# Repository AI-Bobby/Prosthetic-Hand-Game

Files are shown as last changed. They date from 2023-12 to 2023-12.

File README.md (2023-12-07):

# Prosthetic-Hand-Game

This project consists of the mechanical design, electrical design, software design, and using the system of an articulating hand that plays Rock-Paper-Scissors with the user. The hand also has the built-in functionality to control the fingers individually (the ring and pinky finger move together). This was designed around an interest in robotic prosthetics and exoskeletons. 

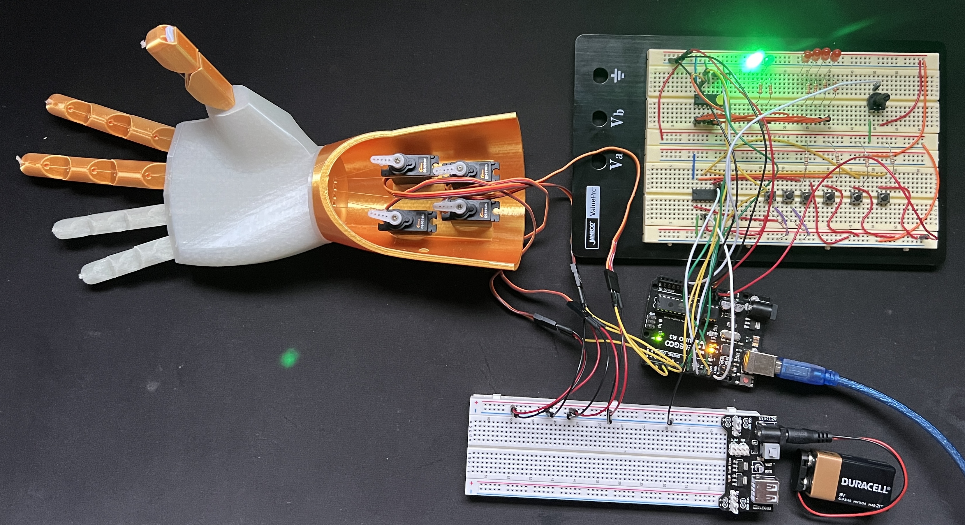
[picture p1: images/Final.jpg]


## 1. Mechanical Design

The mechanical design was based on a normal human hand. The file was modified from an existing design by grossrc on Thingiverse (https://www.thingiverse.com/thing:1691704). Modifications were done by removing the supports that were originally in the design for the circuits. This allows for the arm portion which holds the 4 servo motors used in this design to have free movement when actuating. The .stl files can be seen in the design folder. The 3D printed hands can be seen below:

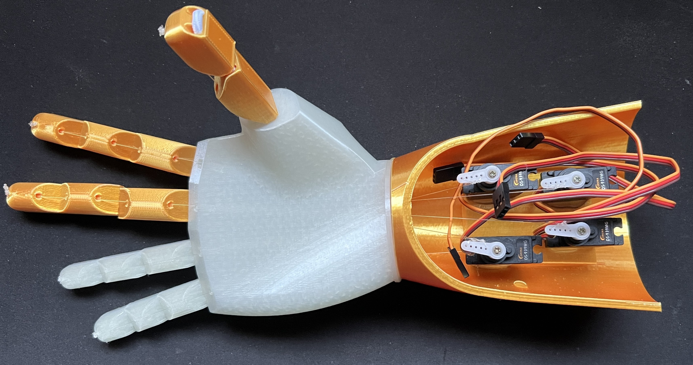
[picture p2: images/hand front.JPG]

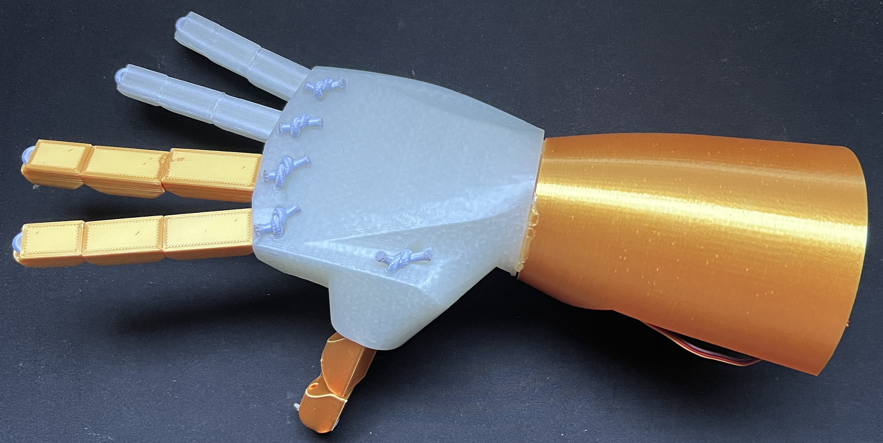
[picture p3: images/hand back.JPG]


The fingers are articulated by 2 things, the fishing line attached to the servo motors, and the nylon string running through the fingers and attached to the hand. The nylon string acts like a tendon that holds the finger in place when not in use. The fishing line is pulled by the servo-motors when they rotate to cause a "muscle" contraction causing the finger(s) to close. The servo motors were positioned to ensure that there would be no collision when the fingers are actuating. The position and the connections of the servo motors can be seen in the image below:

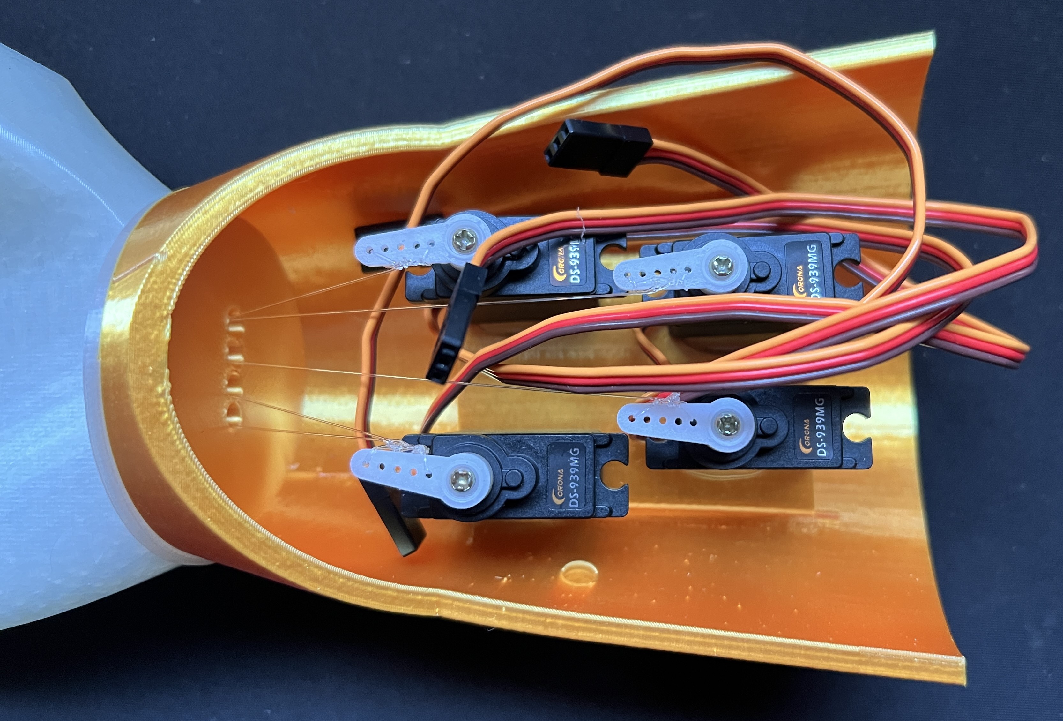
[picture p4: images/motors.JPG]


### BOM

|Part|Description|Qty.|
|:---:|:---|:---:|
|Arduino Uno|Main computational system being used.|1|
|3D Printed Hand|Hand that was 3D printed.|1|
|Nylon String|Nylon string used as tendons in the hand.|5|
|10lb. Test Fishing Line|Fishing line used to act like muscles in the hand.|5|
|DS939MG Digital Servo|Servo motors controlling the fingers.|4|
|CD74HC4051E|8 to 1 Multiplexer reading the control buttons.|1|
|SN74AHC595|8-bit Shift Register controlling the LEDs.|1|
|LED|LEDs giving feedback to the user.|6|
|Button|Buttons used to change output seen by the user.|6|
|220Ω Resistor|Resistors used to limit current to LEDs.|6|
|10kΩ Resistor|Pull-down resistors used with the buttons.|6|
|10kΩ Potentiometer|Potentiometer used to control the position of the servos.|1|
|9V Battery|Battery to supply power to the servo motors.|1|
|Wires|Used to connect components.|58|
|Breadboard|Breadboards used for connecting components together.|3|
|MB102 Power Module|Power Supply Module to supply power to the servos from the 9V battery.|1|
|USB Power Cable|Cable to provide power to the Arduino.|1|

## 2. Electrical Design

For the electrical design an Arduino Uno was used as the microcontroller to run the processes for controlling the hand. The Arduino Uno only has 13 I/O digital pins and 6 analog pins. Based on the original design there would be a total of 6 buttons, 6 LEDs, 4 servo-motors, a potentiometer. Based on these components 16 digital pins would have been needed so the multiplexer and the shift register were added which reduces the number of pins needed. Now the number of digital pins is reduced to 12 digital pins with the shift-register being used for the LEDs and the multiplexer being used for the buttons. The system's wiring diagram can be seen below:

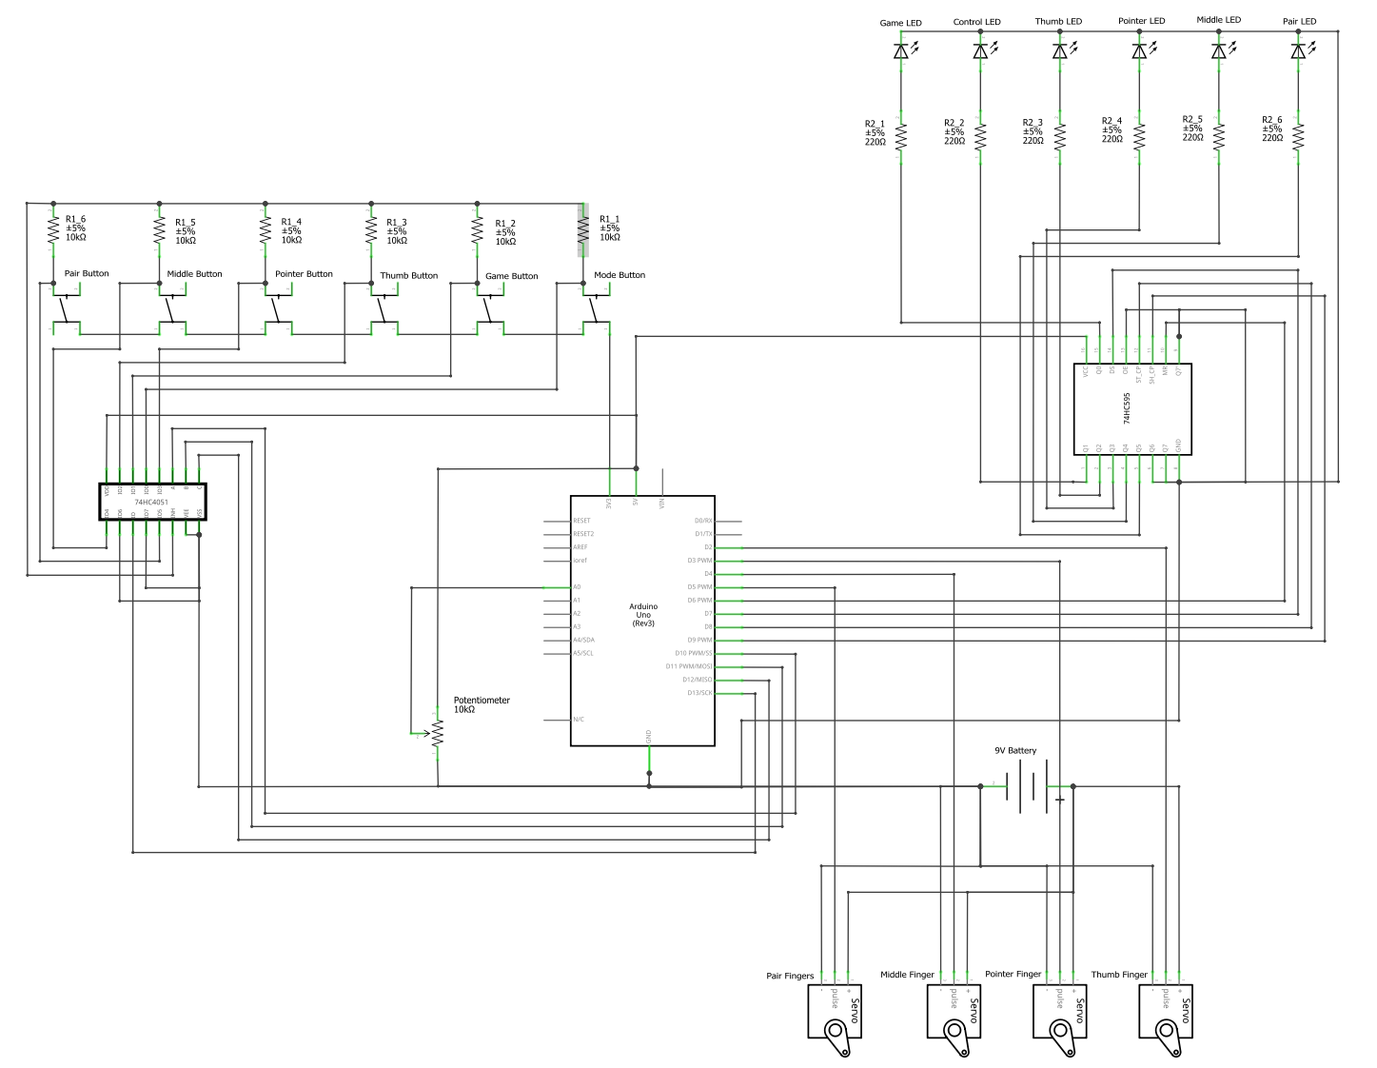
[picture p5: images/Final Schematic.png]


The servo motors are connected to their own separate 9V battery to allow for there to be no current drop if all four of the servo motors are active at the same time. This schematic also shows how the multiplexer and the shift-register are wired to help reduce the number of input wires to the Arduino Uno. The multiplexer has 6 buttons each with their own respective function attached that reads LOW. The buttons have 10kΩ pull-down resistors attached to limit current going into the Arduino and when the button is pressed the Arduino will read HIGH. 

## 3. Software Design

The software design for this system is a simplistic streamlined process to allow for reduced memory usage and ease of use. The file main.cpp in the src folder contains the defined functions of the software running on the Arduino. The code uses enumeration to select the specific case for the multiple switch cases determined by the buttons. Within the code the shift register is used to shift binary strings representing the locations of each of the LEDs to light up based on the specific function being performed. The multiplexer is referenced each loop of the Arduino code and checks each LED to see if a button has been pressed. The pressing of a button influences the specific binary string that is then sent to the shift register to change the LEDs that are lit. The button also determines the mode the system is in as well as the specific finger being controlled.

The code consists of 2 modes and 5 functions: Game, Control, setup, loop, gameMove, updateSystem, and shifter. Each function has its respective repetitive functionality. The mode Game allows for the mode button and the random selection of the hand shape button to be pressed. The game button when pressed uses the microcontroller's clock to get a random seed on each loop so that the selection of the hand shape is completely random. In the Control mode the individual fingers are controlled based on a mapping of the potentiometers analog input and the angles of each servo-motor respectively.  Setup sets the needed pins to their respective I/O setting. Loop checks the button to see if one has been pressed as well as when in the control mode allows for the movement of the fingers based on the reading from the potentiometer mapped to the angles of the servo-motors. The gameMove function randomly chooses the shape for the hand to be performed by the hand and also reset the hand if changed from the control mode to the game mode. The updateSystem function handles the different functionalities based on the button that was pressed. Shifter is a function that sends the binary string to the shift register to change the LED output. 

## 4. Using System

Once the system is wired and powered the system will be in the initial state of Game mode. There are two buttons that have functionality while in Game mode, the game button and the mode button. The game button will cause the hand to give a random hand shape from the selection of Rock, Paper, or Scissors. The mode button will switch the mode from Game to Control or Control to Game based on current state. When the mode is changed the LEDs will change color. The green LED represents game mode, the blue LED represents the control mode and the red LEDs represent the finger being controlled. The finger buttons can be pressed while in game mode but will not change the system into a new state unless in the Control mode. When in control mode the finger buttons can be pressed and this will change the finger being used. The potentiometer can then be used to control the position of the servo which controls the fingers position. If the game button is pressed then nothing will happen because the system is in control mode. The buttons and LEDs can be seen labeled in the wiring schematic above and in the system image below:

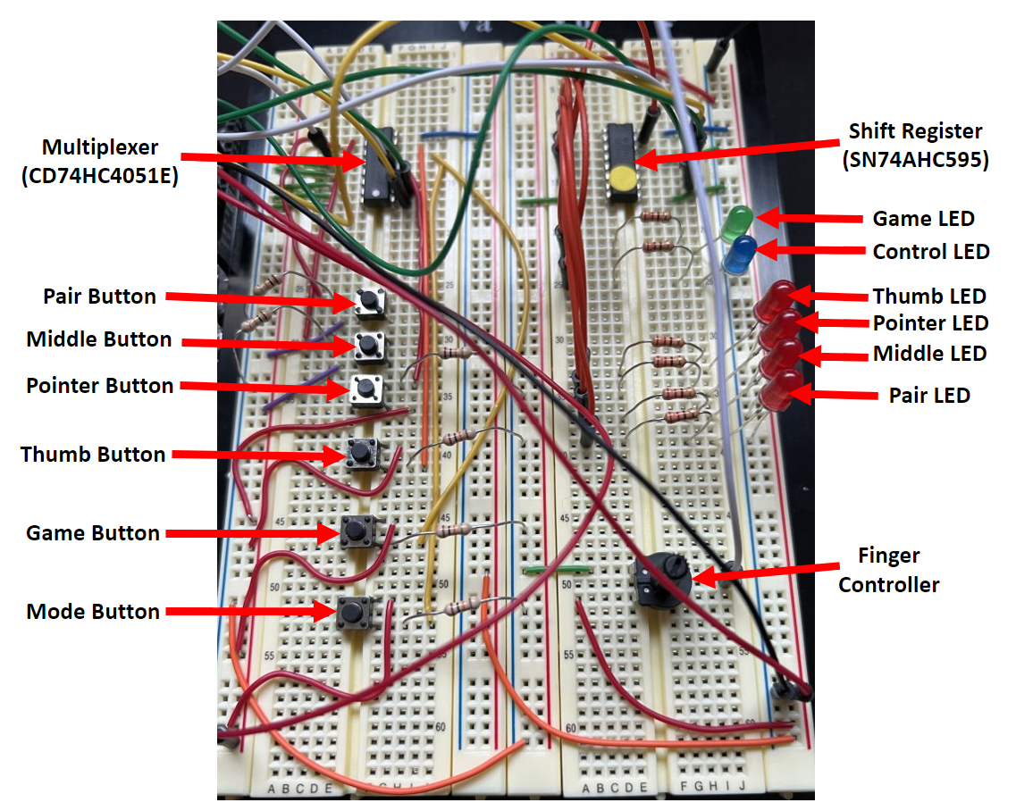
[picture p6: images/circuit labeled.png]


### 4.1 Limitations

The current system has 2 limitations:
1) It was found that the lifespan on a 9V battery is very short because the servo motors when all in use can draw up to ~1A of current which the 9V battery that has 540mAh can not sustain. To circumvent this issue a 5V power supply at 2A was used and allowed for the use of the system without any current drops.
2) During the contraction of the fingers where they should close the fingers do actuate but they do not fully close as a normal hand would. This is caused by the distance of actuation by the motor not being sufficient to fully pull the finger. This can be fixed by either using a longer motor arm horn or using a different actuator. An actuator that could give a larger actuation distance would be a linear actuator where rotation would not have to be considered. The tension that is on the fishing line also plays an effect. Fishing line has an elastic characteristic that needs to be loaded to allow for the actuation of the motor to be seen by the finger. This could be fixed by introducing a string that has much less elasticity.

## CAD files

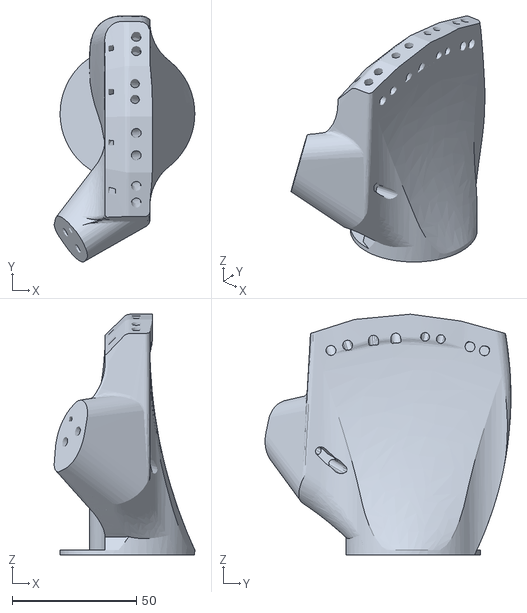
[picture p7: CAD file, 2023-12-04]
design/Hand.stl
56.5 x 98.9 x 96.8

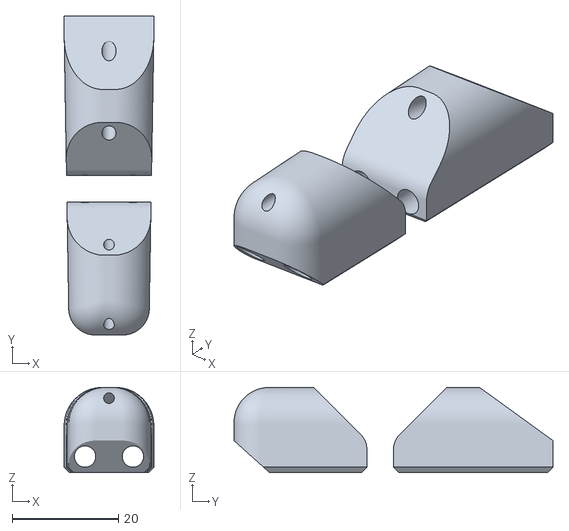
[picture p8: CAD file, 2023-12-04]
design/Thumb.stl
17.0 x 60.0 x 16.0

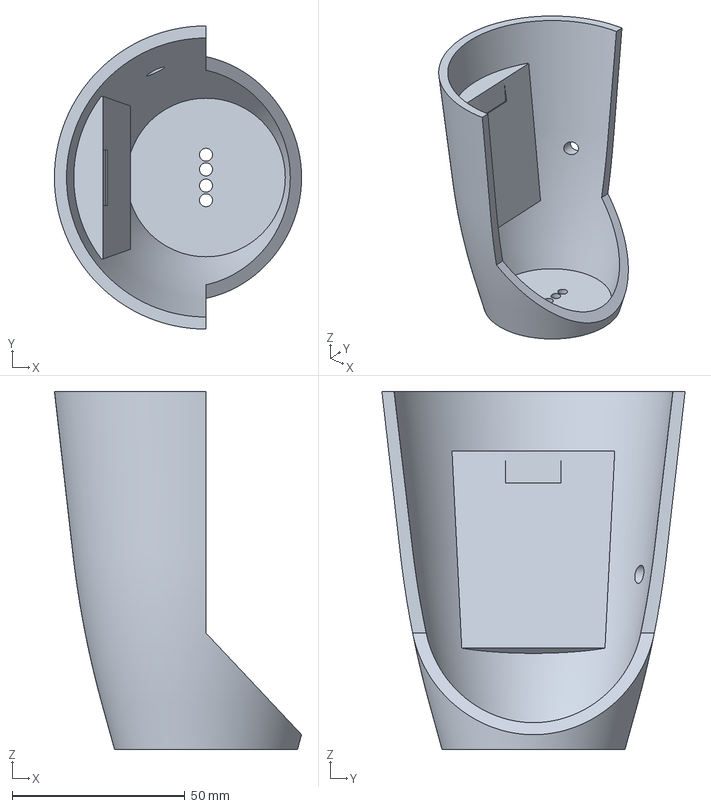
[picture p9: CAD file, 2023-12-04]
design/Arm.3mf
71.5 x 87.7 x 103.6 mm

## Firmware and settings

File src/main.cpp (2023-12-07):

#include <Arduino.h>
#include <avr/pgmspace.h>
#include <Servo.h>

#define s0 10
#define s1 11
#define s2 12
#define SIG_pin 13
#define latch 8
#define clock 9
#define data 7
#define clear 6
#define pot A0

byte channels [8] = {0};

// enumerate two modes (Game, Control)
typedef enum{Game, Control} unoMode;
// enumerate three choices (Rock, Paper, Scissors)
typedef enum{Rock, Paper, Scissors, Reset}gameChoice;
// enumerate four fingers (Thumb, Pointer, Middle, Pair)
typedef enum{Thumb, Pointer, Middle, Pair}fingerSelect;

// four servo objects to control thumb, pointer, middle, and ring/pink fingers
Servo thumb, pointer, middle, pair;

// define byte string for LED outputs {Game, Control Thumb, Control Pointer, Control Middle, Control Pair}
const byte PROGMEM fingerLED[5] = {0b10000000, 0b01100000, 0b01010000, 0b01001000, 0b01000100};
byte LED_byte;

// initialize mode, choice, and finger variables
unoMode mode = Game;
gameChoice choice = Rock;
fingerSelect finger = Thumb;

void gameMove();
void updateSystem(byte idx);
void shifter();

void setup() {

  Serial.begin(9600);

  //Set POT and Mux pin to input
  pinMode(pot, INPUT);
  pinMode(SIG_pin, INPUT);

  //Set mux pins to output
  pinMode(s0, OUTPUT);
  pinMode(s1, OUTPUT);
  pinMode(s2, OUTPUT);

  //Set shift register pins to output
  pinMode(latch, OUTPUT);
  pinMode(clock, OUTPUT);
  pinMode(data, OUTPUT);
  pinMode(clear, OUTPUT);

  // attach servos to pins
  thumb.attach(2);
  pointer.attach(3);
  middle.attach(4);
  pair.attach(5);

  // initialize clear shift register and set LEDs to Game
  digitalWrite(clear, LOW);
  digitalWrite(clear, HIGH);
  LED_byte = pgm_read_byte(&fingerLED[0]);
  shifter();

  // initialize servos to default position
  thumb.write(170);
  delay(200);
  pointer.write(170);
  delay(200);
  middle.write(10);
  delay(200);
  pair.write(10);
  delay(200);
  thumb.detach();
  pointer.detach();
  middle.detach();
  pair.detach();


}

void loop() {
  randomSeed(millis());

  // read all buttons 
  for (byte idx = 0; idx < 8; idx++){
    // set mux to read each button for HIGH and LOW through bitwise AND
    digitalWrite(s0, HIGH && (idx & B00000001));
    digitalWrite(s1, HIGH && (idx & B00000010));
    digitalWrite(s2, HIGH && (idx & B00000100));
    channels[idx] = digitalRead(SIG_pin);
    if (channels[idx] == HIGH){
      updateSystem(idx);
      delay(100);
    }
  }

  // read potentiometer and control servos when in Control mode
  if (mode == Control){
    int val = analogRead(pot);
    Serial.println(val);
    byte angle = 0;
    switch (finger){
      case Thumb:
        angle = map(val, 0, 1023, 170, 10);
        thumb.attach(2);
        thumb.write(angle);
        delay(50);
        thumb.detach();
        break;
      case Pointer:
        angle = map(val, 0, 1023, 170, 10);
        pointer.attach(3);
        pointer.write(angle);
        delay(50);
        pointer.detach();
        break;
      case Middle:
        angle = map(val, 0, 1023, 10, 170);
        middle.attach(4);
        middle.write(angle);
        delay(50);
        middle.detach();
        break;
      case Pair:
        angle = map(val, 0, 1023, 10, 170);
        pair.attach(5);
        pair.write(angle);
        delay(50);
        pair.detach();
        break;
    }
  }

}

//  thumb:   (170 erect / 10 bent)
//  pointer: (170 erect / 10 bent)
//  middle:  (10 erect / 170 bent)
//  pair:    (10 erect / 170 bent) 

//define servo positions for each game choice
void gameMove(){
  switch (choice){
    case Rock:
      pair.attach(5);
      middle.attach(4);
      pointer.attach(3);
      thumb.attach(2);

      pair.write(170);
      delay(200);
      middle.write(170);
      delay(200);
      pointer.write(10);
      delay(200);
      thumb.write(10);
      delay(2000);
      thumb.write(170);
      delay(200);
      pointer.write(170);
      delay(200);
      middle.write(10);
      delay(200);
      pair.write(10);
      delay(500);

      thumb.detach();
      pointer.detach();
      middle.detach();
      pair.detach();

      break;
    case Paper:
      thumb.attach(2);

      thumb.write(10);
      delay(2000);
      thumb.write(170);
      delay(500);

      thumb.detach();
      break;
    case Scissors:
      pair.attach(5);
      thumb.attach(2);

      pair.write(170);
      delay(200);
      thumb.write(10);
      delay(3000);
      thumb.write(170);
      delay(200);
      pair.write(10);
      delay(500);

      thumb.detach();
      pair.detach();
      break;
    case Reset:
      thumb.attach(2);
      pointer.attach(3);
      middle.attach(4);
      pair.attach(5);

      thumb.write(170);
      delay(200);
      pointer.write(170);
      delay(200);
      middle.write(10);
      delay(200);
      pair.write(10);
      delay(500);

      thumb.detach();
      pointer.detach();
      middle.detach();
      pair.detach();
      break;
  }
}

// update system based on button presses
void updateSystem(byte idx){
  switch (idx){
    case 0:
      if (mode == Game){
        mode = Control;
        LED_byte = pgm_read_byte(&fingerLED[1]);
        finger = Thumb;
        shifter();
      }
      else{
        mode = Game;
        LED_byte = pgm_read_byte(&fingerLED[0]);
        shifter();
        choice = Reset;
        gameMove();
      }
      break;
    case 1:
      if (mode == Game){
        byte rand_idx = random(0, 3);
        if (rand_idx == 0){choice = Rock;}
        else if (rand_idx == 1){choice = Paper;}
        else if (rand_idx == 2){choice = Scissors;}
        gameMove();
      }
      else{}
      break;
    case 2:
      if (mode == Game){}
      else{
        LED_byte = pgm_read_byte(&fingerLED[1]);
        finger = Thumb;
        shifter();
      }
      break;
    case 3:
      if (mode == Game){}
      else{
        LED_byte = pgm_read_byte(&fingerLED[2]);
        finger = Pointer;
        shifter();
      }
      break;
    case 4:
      if (mode == Game){}
      else{
        LED_byte = pgm_read_byte(&fingerLED[3]);
        finger = Middle;
        shifter();
      }
      break;
    case 5:
      if (mode == Game){}
      else{
        LED_byte = pgm_read_byte(&fingerLED[4]);
        finger = Pair;
        shifter();
      }
      break;
  }
}

// change shift register output based on defined byte string
void shifter(){
  digitalWrite(latch, LOW);
  shiftOut(data, clock, LSBFIRST, LED_byte);
  digitalWrite(latch, HIGH);
}
